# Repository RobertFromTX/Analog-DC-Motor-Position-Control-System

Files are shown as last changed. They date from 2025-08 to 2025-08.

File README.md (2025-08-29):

# Analog PI Control for Basic Positioning of a Brushed DC Motor

## Video Demo
https://github.com/user-attachments/assets/2bba8920-0b15-401e-9de0-5b88466c60b8

If the video does not play, refresh the page.

## Project Overview and Goals
This is a project I completed at the beginning of Summer 2025. Essentially it turns a brushed DC motor into a servo motor, though it cannot produce the torque of one. Given an input voltage in the range of 0V-5V, it positions the motor to an angle proportional to the input voltage. For example, 0V would position the motor at 0 degrees while 2.5V would position the motor at 180 degrees. The controller is built with op-amps and an encoder. Initially, I wanted to create a PID controller, but the signals from the derivative term were often too noisy. As a result, I ended up with a PI controller. Nevertheless, a PI controller is more than sufficient to control the position of the motor.

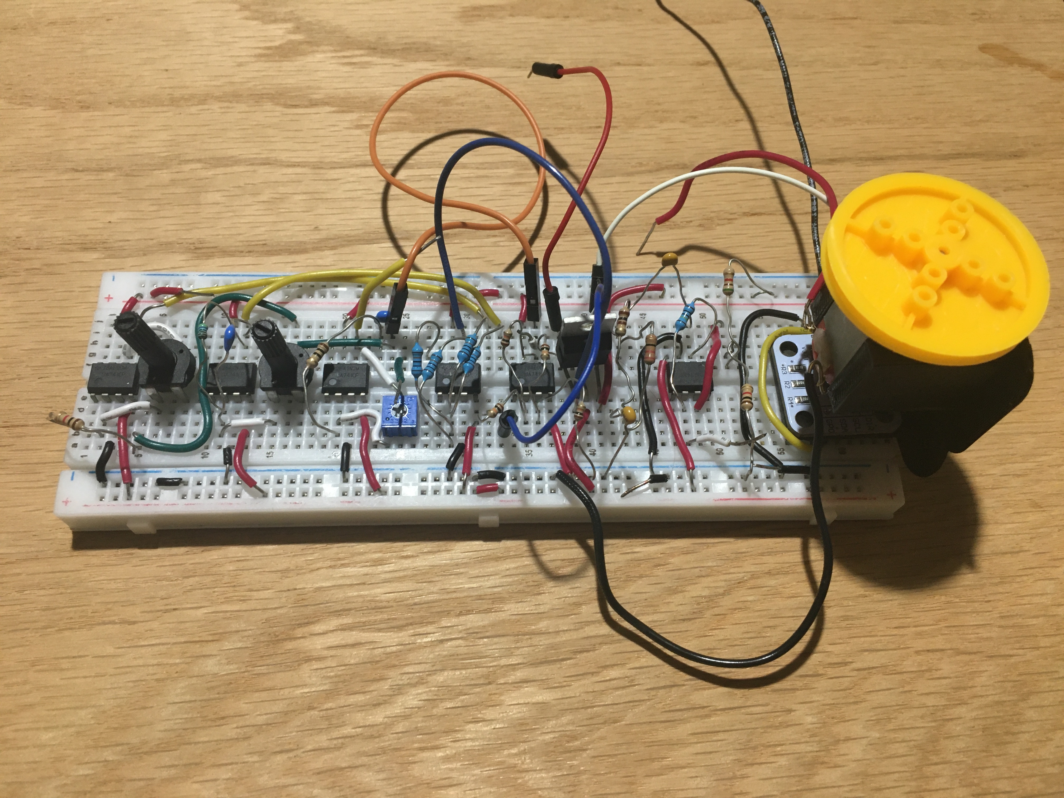
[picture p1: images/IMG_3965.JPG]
Motor Controller


## Design
There were two design constraints that I set for this project. The first design constraint was that I could only use parts I already had on hand. The second design constraint was that only one breadboard can be used to place the circuit components onto.

### Preliminary Design
The first step taken in the design phase was to plan how the overall structure of the system should be to accomplish the control task. The overall system requires three components: an actuator, a sensor, and a PI Controller. The sensor's task is to determine the angular position of the motor, which the PI controller will use to correct the position of the motor. Below is a block diagram of the preliminary design. <br>
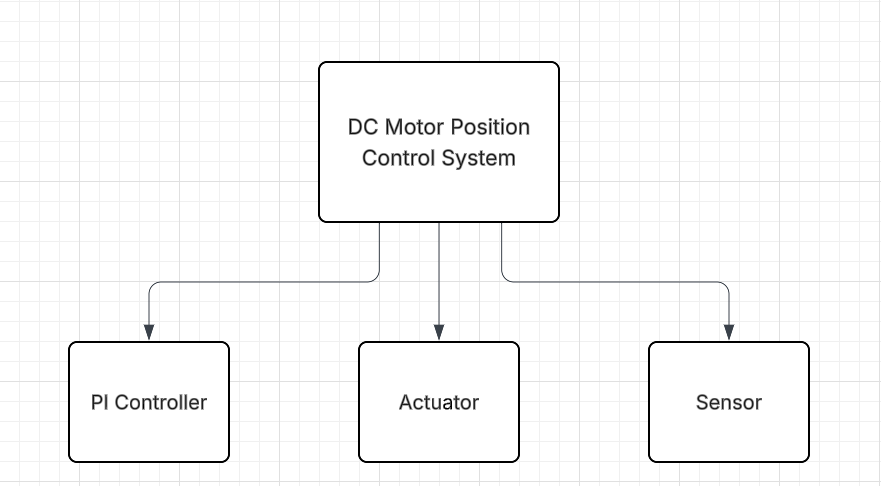
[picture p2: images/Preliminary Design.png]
Preliminary Design Diagram


### Detailed Design
After the components of the system have been identified, the next step is to create the actual designs of each component.

**Motor:**<br>
For the motor, a simple brushed DC motor was chosen.

**Sensor:**<br>
For the sensor, the [AS5600](https://www.amazon.com/Alinan-Magnetic-Precision-Induction-Measurement/dp/B09QYC916Q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) magnetic encoder breakout board was chosen. The key reason this sensor was chosen is that it outputs a voltage proportional to the angular position. Most other encoders send pulses that are difficult to process without a microprocessor. There are many ways to wire and configure this device, but I won't go into it here since only the output of this "blackbox" is relevant for the project. However, you are curious, [here](https://www.youtube.com/watch?v=_BwtM5f6AQ0) is how I did it (though it is far from the best way since it degrades the device quickly).

**PI Controller:**<br>
Designing the PI Controller was easily the most difficult part of this project. The approach that I used was to break the PI Controller down into its sub-components and test each individually. In total I identified 5 sub-components as I progressed through the PI controller:

1. Subtraction op-amp circuit
2. Proportional op-amp circuit
3. Lossy Integrator op-amp circuit
    * Why am I using a lossy integrator opposed to a pure integrator? The reason is because if the output of the encoder has very low frequency, the output of the pure integrator could grow very fast. With DC input signals, the pure integrator output will ramp unboundedly. The lossy integrator is a lowpass filter that levels off the gain as super low frequencies are approached. For example, every input signal below 31.8 Hz will be amplified by roughly the same amount of gain if the cutoff frequency is 31.8 Hz.
4. Summing op-amp circuit
5. Buffer to drive DC motor
    * Since the only op-amp I have used for all of the circuits up to this point is the [UA741CP](https://www.ti.com/lit/ds/symlink/ua741.pdf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), there is nothing that has the capability to drive the brushed DC motor. While the UA741CP op-amp can supply a maximum of 40 uA of current, the motor will need much more. The [TDA2030A](https://www.st.com/resource/en/datasheet/cd00000129.pdf) is able to supply up to 3.5A. This is enough current for this motor, but there must be caution for current spikes. The output current of the TDA2030A is internally limited, which will help prevent the op-amp from blowing up.
    
Before I finalized my component values for each op-amp configuration, I ran simulations using LTspice to ensure that the circuits behaved desireably. Then, I created a model in simulink to ensure that I can correctly integrate each component together. Below is my Simulink block diagram.
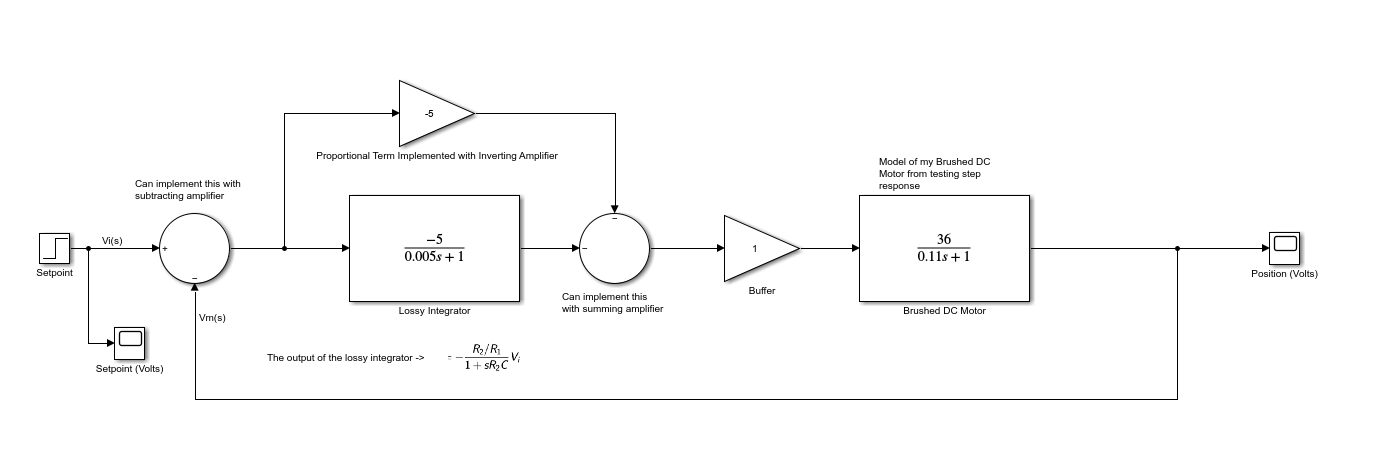
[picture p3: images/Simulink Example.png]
Simulink Block Diagram
 <br>
Now that I determined that the system can be integrated properly, I designed a circuit by selecting passive component values and creating a schematic in Kicad. Below is a schematic of the final circuit.
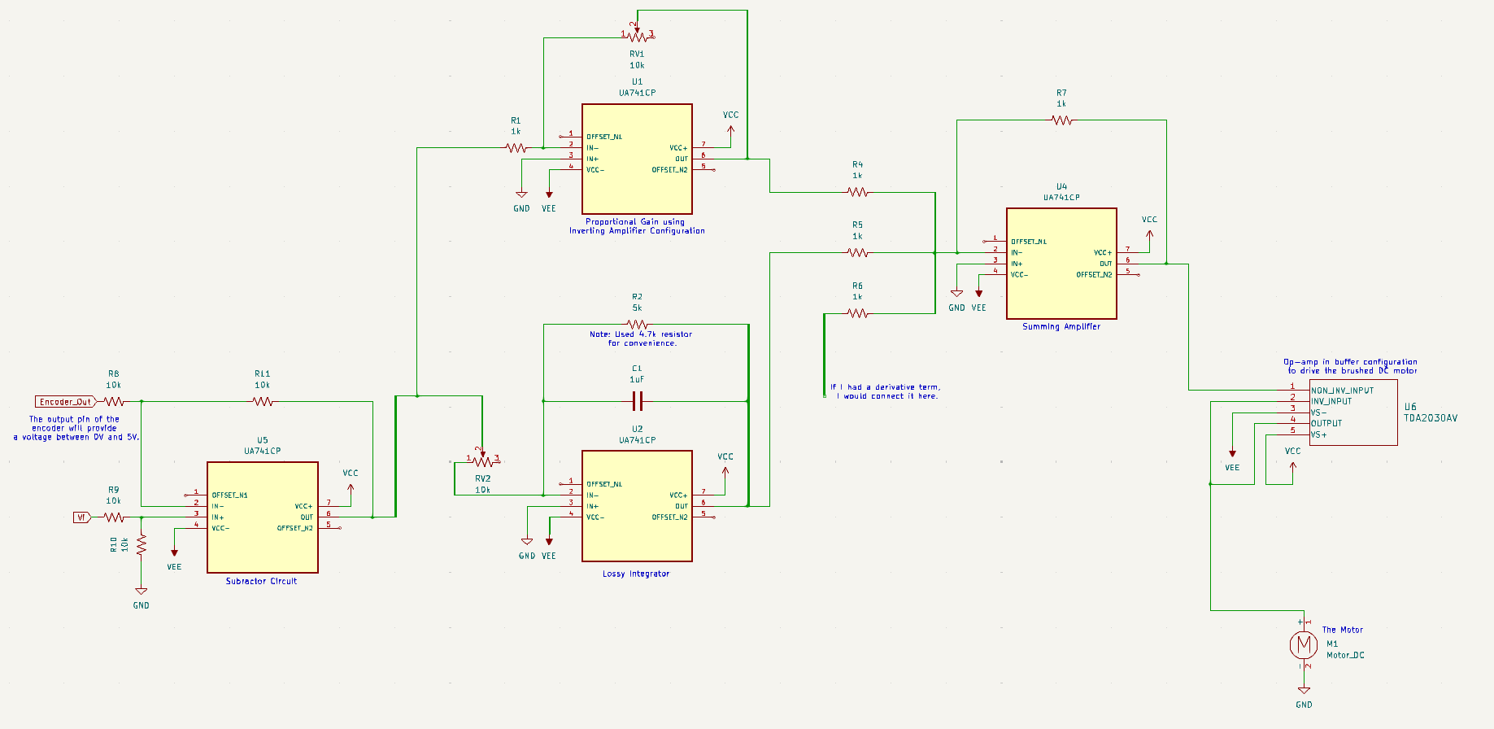
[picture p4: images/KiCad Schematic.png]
KiCad Schematic

## Results and Takeaways
In the end, I basically ended up with a servo motor. The system did behave how I desired, but I know that there are not many use cases for it besides educational purposes since the controller is quite heavy while the motor produces very little torque. Other brushed DC motors can be substituted easily, which is a perk of my controller.

I found the control problem to be quite easy. Unlike a drone or a self-balancing robot, this system is not inherently instable. As a result, there is not much tuning required to get a minimally functional system. On the other hand, the circuitry was quite a challenge. There were tons of roadblocks when it came to signal integrity. There were many things creating undesirable noise in my system, making it not work at all. Small things such as having a mouse wire near my system would generate a lot of noise, and I had to use my oscilloscope on multiple occassions to finally get my system working. As a result, I decided that my next few projects would be based on microcontrollers since it is much easier to create reliable systems that are based on microcontrollers.

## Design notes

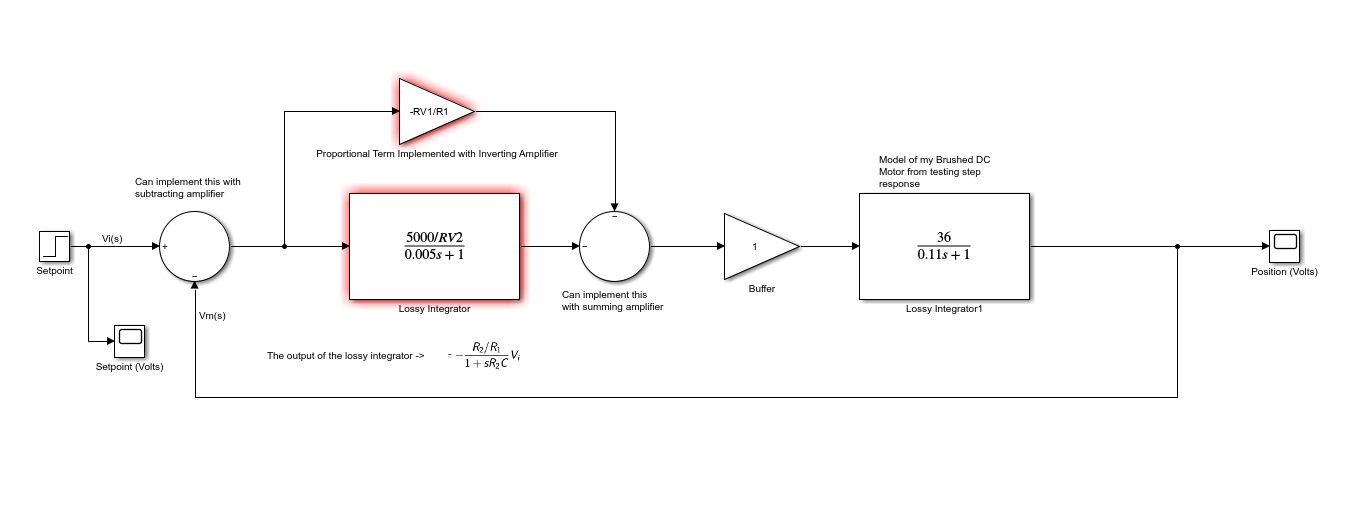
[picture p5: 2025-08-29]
images/Simulink Variable.png
